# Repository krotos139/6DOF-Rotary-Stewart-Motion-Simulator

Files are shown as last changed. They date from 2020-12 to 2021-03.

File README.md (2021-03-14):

# !!! WARNING !!!

Hey. I'm making 6dof project base of https://github.com/knaufinator/6DOF-Rotary-Stewart-Motion-Simulator/tree/master/Technical

This is a DANGEROUS project, and if absolute care is not taken you will be injured or killed.

Project isn't finished yet. I will place all data to this repo.

# Experiments one

We made PCB from Christopher Knauf. And we can to control one AC motor driver:

<a align="center" href="https://youtu.be/x41-dcpQG4Y
" target="_blank"></a>

# Projects Included
These are the components of the project that are included in this repository

## Technical 

I made all draws in Kompas 3D. I will make drawings in the future.

This is current project:

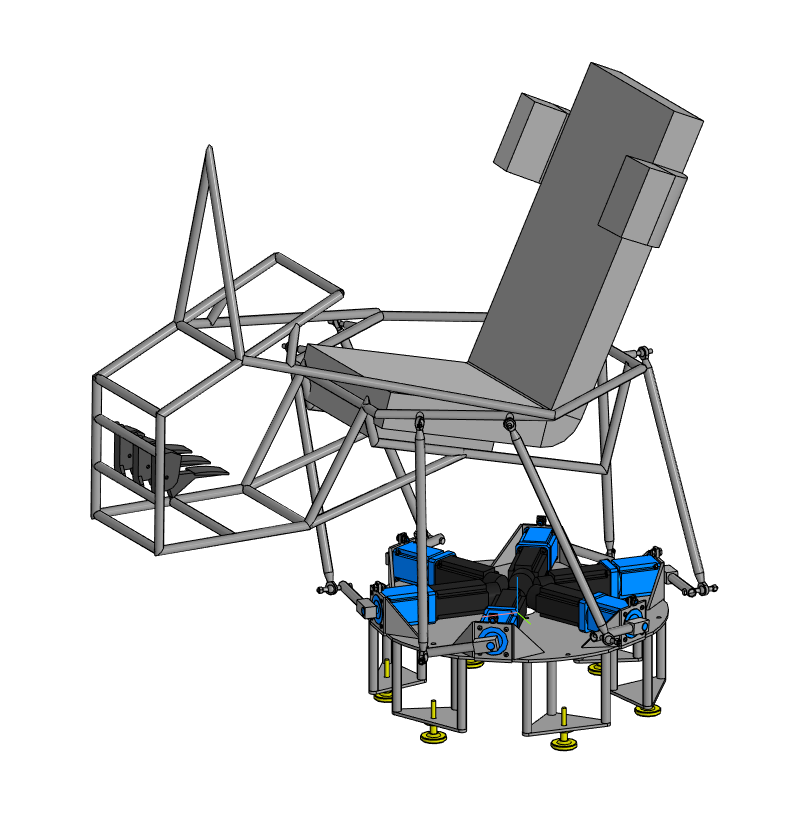
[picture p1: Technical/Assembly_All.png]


## Controller
This is an ESP32 Arduino project. This interfaces with the PC through software like simtools, after correctly configuring. This project utilizes both ESP32 cores in order to maximize refresh rates to 1000Hz, or 1ms interval. A custom MCP23S17 library is included so the outputs of all 6 motors can be set at one time instead of setting them individually, this saves time and allows for more pulses per second. This increase allows for higher movement precision on the rotational arm. There is also a filter library included, this is still in early testing.

## Simtools interface setup
Config for PC to ESP32 USB-> Serial connection within simtools, simtools will be configured to send the 6 axis parameters over to the ESP32 every 1 ms. Over a 250000 baud connection. The packet consists of 6 - 12 bit values, delimited by comma and ended by a "X" Character to signal the ESP32 that the packet is done. 

For simtools you encode the axis representations of x,y,z,Ry,Rx,RZ  with the configuration"Interface - Output" = \<Axis1a>,\<Axis2a>,\<Axis3a>,\<Axis4a>,\<Axis5a>,\<Axis6a>X   

With these settings the software package Simtools or any other custom application may communicate and command the simulator platform to move.



## Controller Schematics

We developed our controller board with optocoupler:

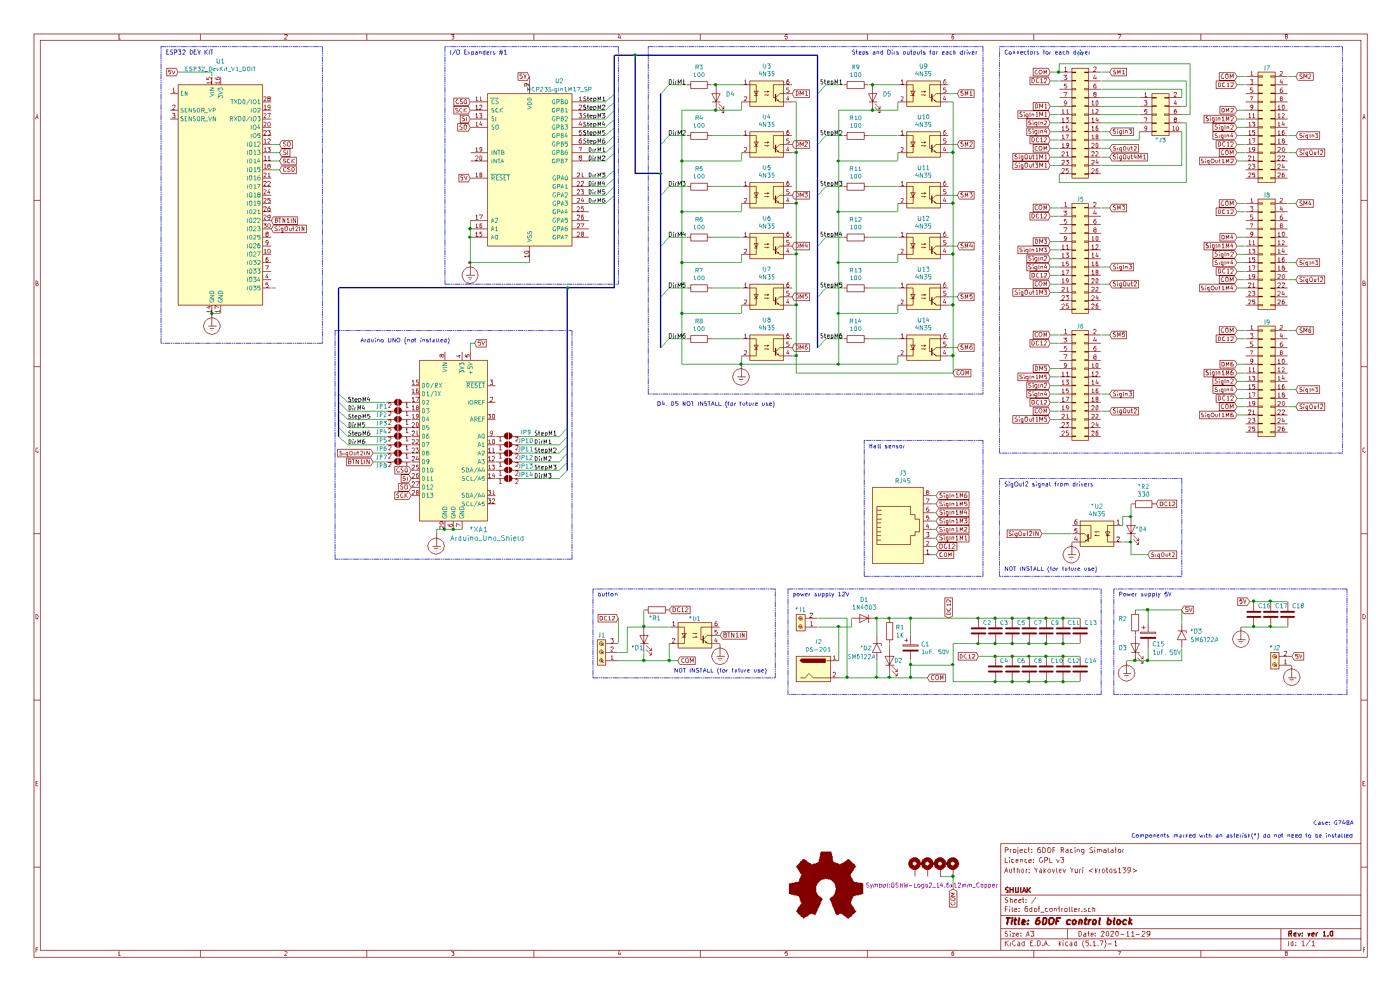
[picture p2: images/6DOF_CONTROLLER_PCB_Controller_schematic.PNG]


We use sensor bord from Christopher Knauf: 

## Controller PCB

We have a problem with USB interface. We start to do second PCB:

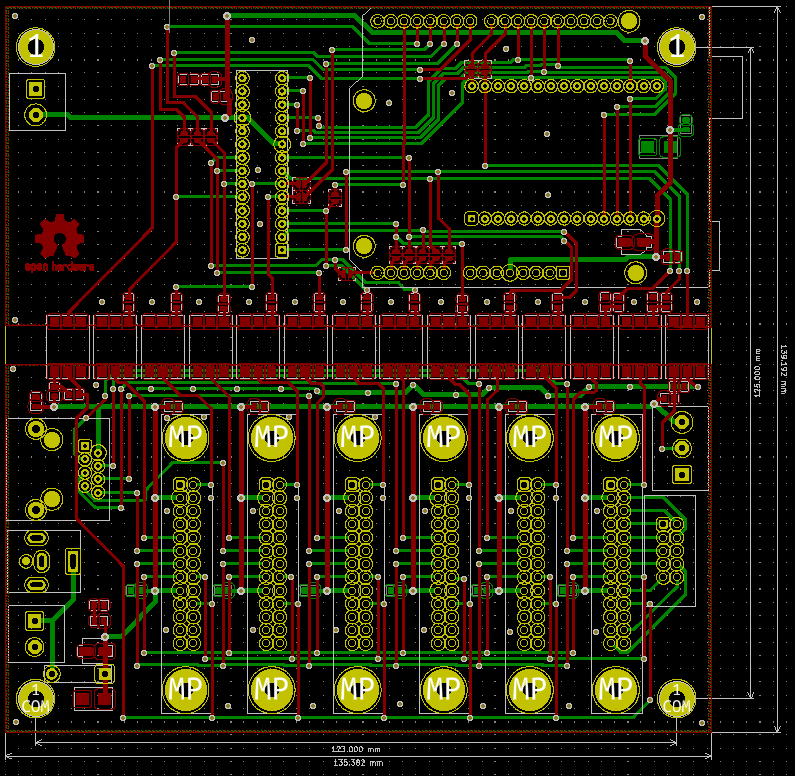
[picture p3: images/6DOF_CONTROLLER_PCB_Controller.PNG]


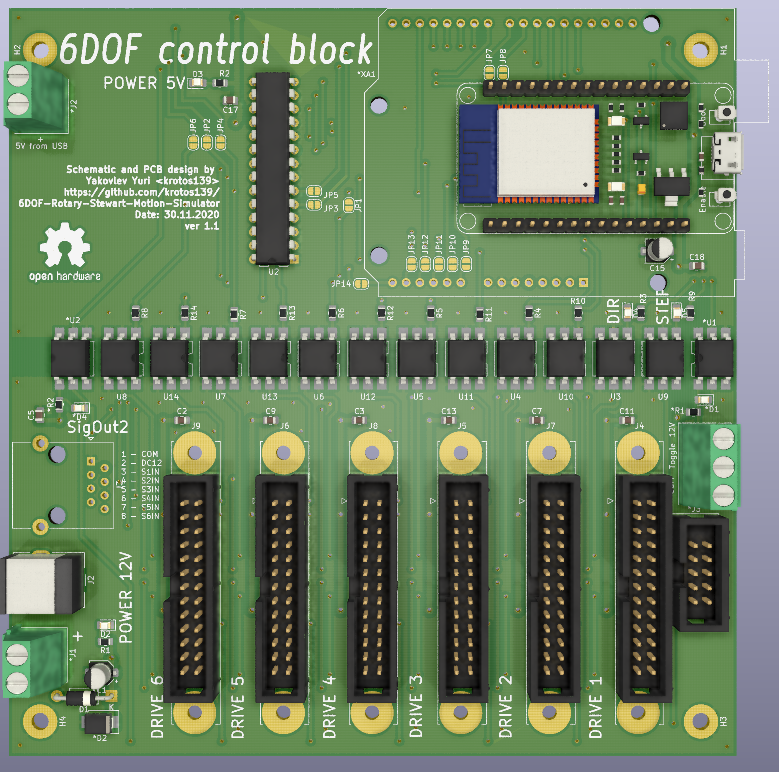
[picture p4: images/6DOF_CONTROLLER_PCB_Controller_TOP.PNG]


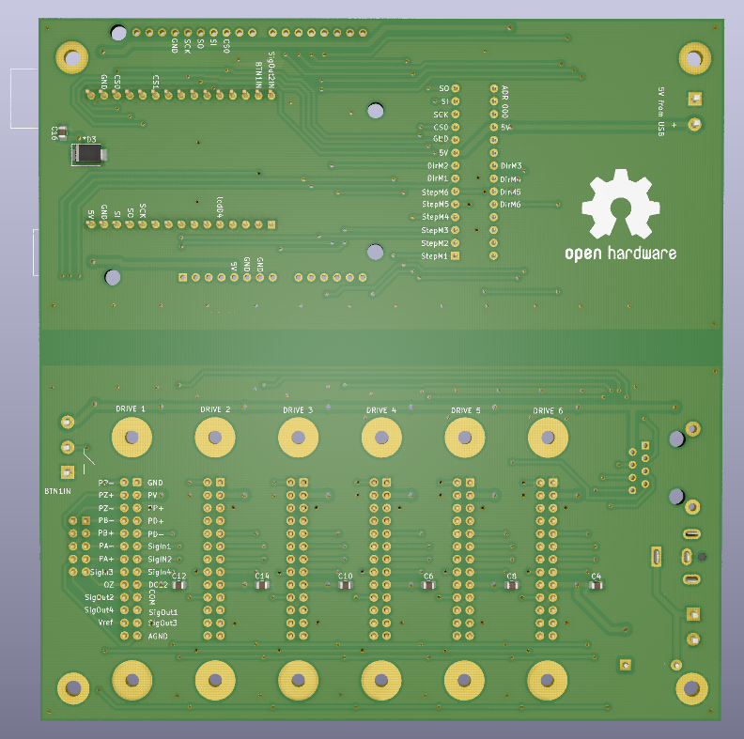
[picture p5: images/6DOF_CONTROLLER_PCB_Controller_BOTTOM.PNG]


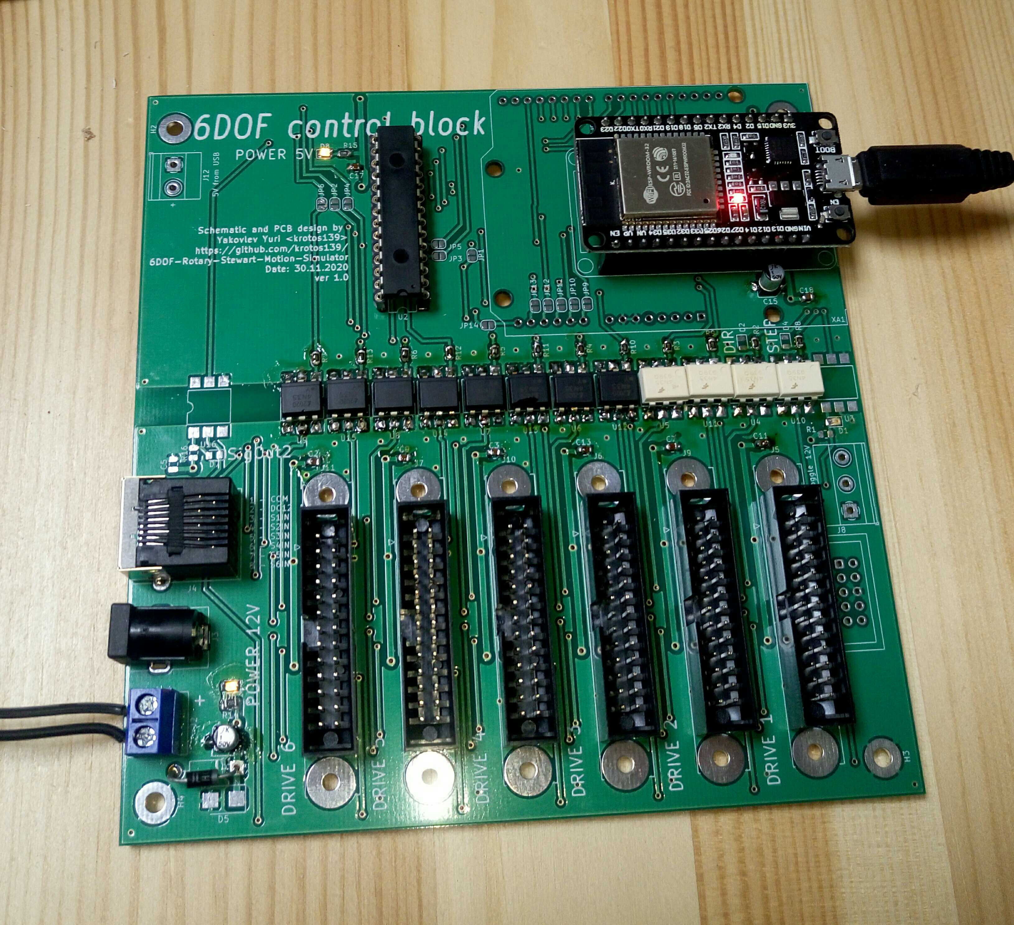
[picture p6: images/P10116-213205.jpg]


## TDD MMOS Schematics

We developed our TDD MMOS board with optocoupler:

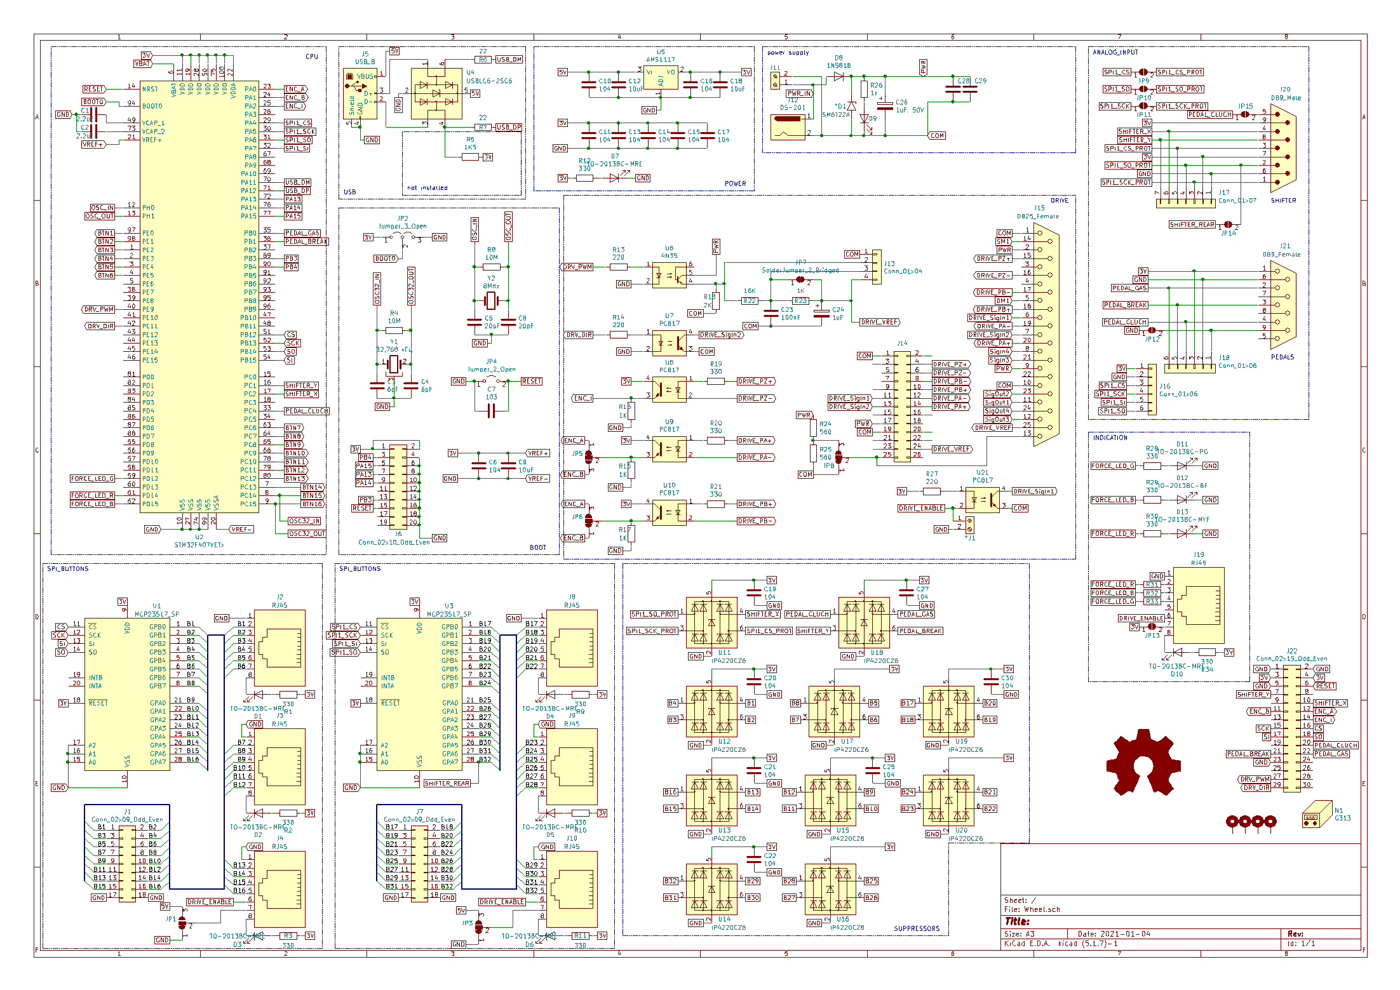
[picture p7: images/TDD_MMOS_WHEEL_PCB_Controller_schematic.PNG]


## TDD MMOS PCB

We redesigned PCB for TDD MMOS. We've added optocouplers and second port extender.

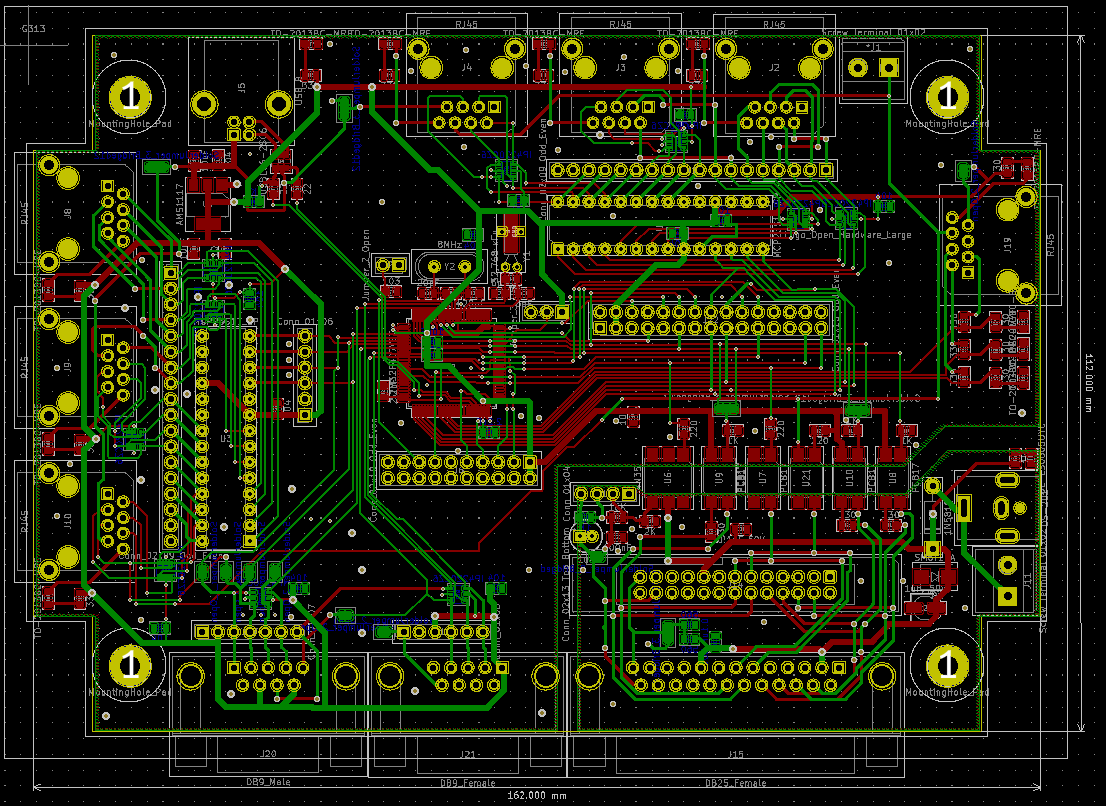
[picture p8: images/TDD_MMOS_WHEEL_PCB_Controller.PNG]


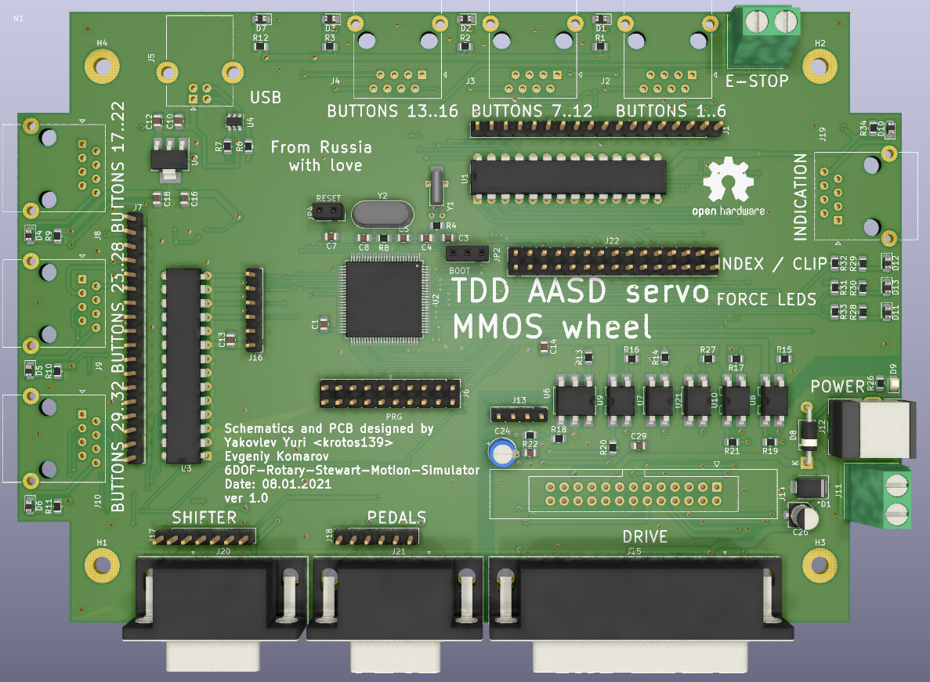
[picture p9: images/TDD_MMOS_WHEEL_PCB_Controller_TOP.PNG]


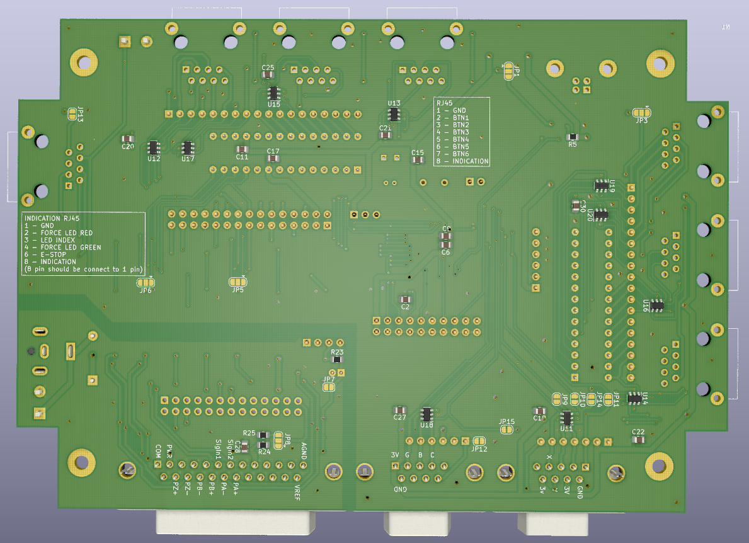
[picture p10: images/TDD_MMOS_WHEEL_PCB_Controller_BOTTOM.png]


## Pedal's PCB

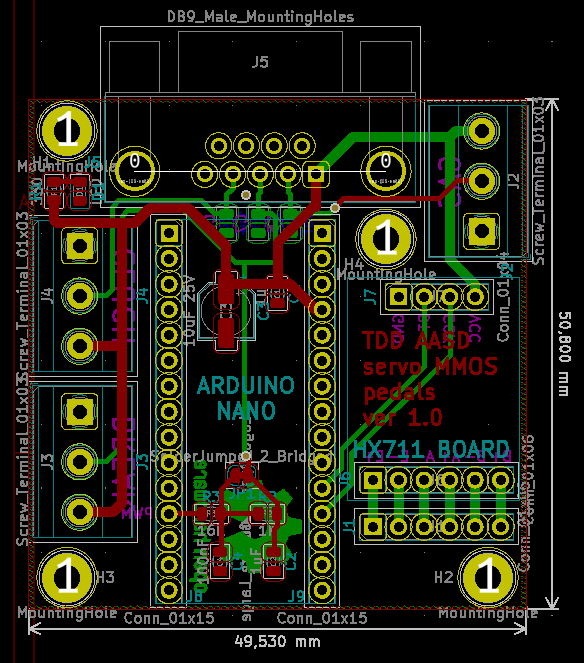
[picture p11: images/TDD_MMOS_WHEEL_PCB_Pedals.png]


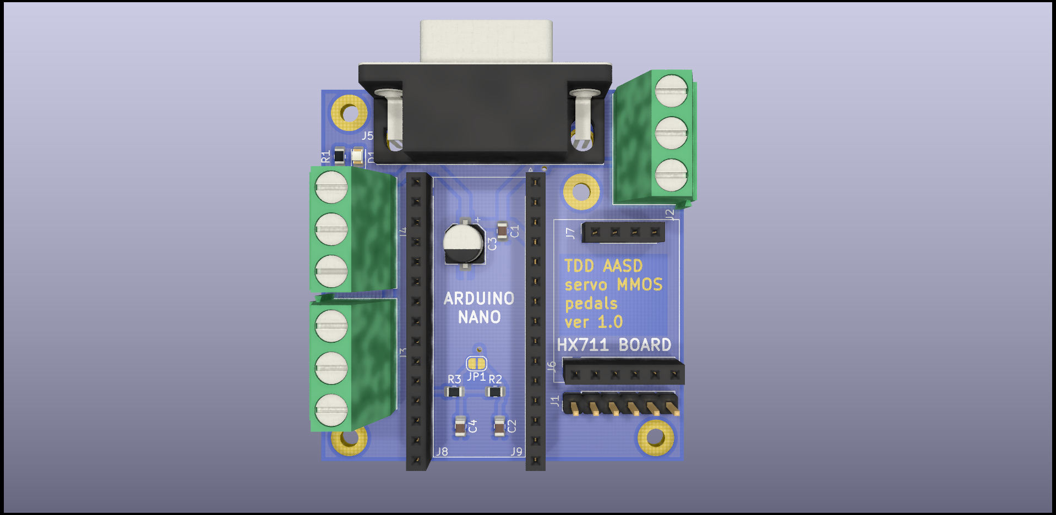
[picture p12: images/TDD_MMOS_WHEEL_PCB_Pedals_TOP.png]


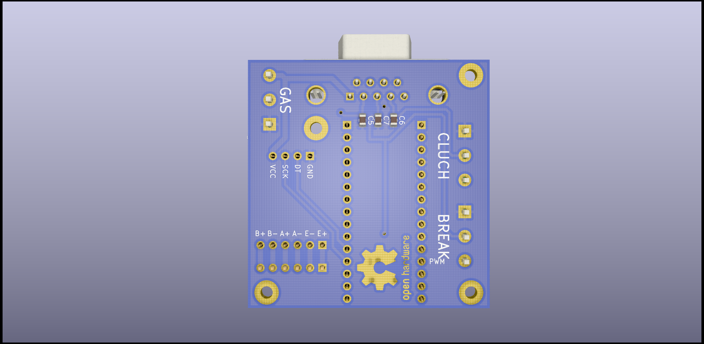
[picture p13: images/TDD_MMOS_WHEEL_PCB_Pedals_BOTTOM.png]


## Platform Test Application
.Net Application for testing position limits and speed of platform. Allows for manual setting of each DOF / Axis. As well works with XBOX360 controller through the PC USB wireless adapter.

# Parts
These are some key parts I used, others can be used in their place, but variations of the AC Servo motor may not be compadible with the PCB, and may require a modified PCB schematic. 

## Electric components

* [AC Ammeter Voltmeter](https://www.aliexpress.com/item/4000589056233.html?spm=a2g0s.9042311.0.0.40e133edW2JAK5)

## Controller 
Main components on the PCB
* [ESP32 Dev board](https://aliexpress.ru/item/1005001267643044.html?spm=a2g0s.9042311.0.0.40e133edW2JAK5) - ESP32 Dev kit
* [MCP23S17-E/SP](https://www.chipdip.ru/product1/8002981432)
* [3.3V to 5V TTL Shifter Module](https://aliexpress.ru/item/32825755943.html?spm=a2g0s.9042311.0.0.40e133edW2JAK5)
* [NJK-5002C NPN NO（Normally Open)Hall Effect Sensor Switch](https://aliexpress.ru/item/32922514991.html?spm=a2g0s.9042311.0.0.40e133edW2JAK5)
* [IDC BOX HEADER 2X13 26PIN](https://aliexpress.ru/item/33009552726.html?spm=a2g0s.9042311.0.0.40e133edW2JAK5)
* [RJ45](https://aliexpress.ru/item/4000226018964.html?spm=a2g0s.9042311.0.0.40e133edW2JAK5)
* [KF301 HEADER 3 pin](https://aliexpress.ru/item/4001057723206.html?spm=a2g0s.9042311.0.0.40e133edW2JAK5)
* [KF301 HEADER 2 pin](https://aliexpress.ru/item/4001057742092.html?spm=a2g0s.9042311.0.0.40e133edW2JAK5)
* [Female Pin Header Connector](https://aliexpress.ru/item/32964870579.html?spm=a2g0s.9042311.0.0.40e133edW2JAK5)

PCB
* [Gerber files](Controller PCB Gerber/)
* [PCB Manufacturer](https://www.rezonit.ru/)

## Base
- Steel plate 8 mm thick 31” diameter
- 6 - Coupler https://amzn.to/2slOiIa

## Drive
* [6 - 750w AC servo Motors](https://www.aliexpress.com/item/32844239563.html)
* [6 - 50:1 Planetary Gears](https://www.aliexpress.com/item/32967571001.html)
*Note ensure planetary gear input diameter matches up to both the motor as well with the coupler output diameter when ordering from Aliexpress

## Connecting Arms

* [12 - Swivel head SA 12mm](https://podtrade.ru/product/42564/)
* [12 - M12 to M10 High Misalignment Angle Reducer Reducers Spacers Rod End Joint](https://www.ebay.com/itm/184116983786)
* 6 - 25x179 Steel pipe

## Swing Arms
* 6 - 25x22mm_clamp2.m3d
* 6 - 25x560 Steel pipe

## Frame 
* 16.5 meters of steel pipe

## Chassis
* [Vesa Monitor mount](https://amzn.to/2TmVS0f)
* [Coped Steel Bungs](https://amzn.to/2TGOcoo)
* [1" OD X .870 ID X .065 Wall Steel tubing](https://amzn.to/3au4FCQ)

## Extras as built in demonstration video
* [LG 34" Ultrawide](https://amzn.to/2t8YvbC)
* [Thrustmaster T16000M FCS](https://amzn.to/30qkHtY)
* [Wind Generator Fan](https://amzn.to/36W1um9)
* [Wind Generator PWM Control](https://amzn.to/2Ns1anq)
* [Wind Generator 90 Degree angle 3"-> 2" Reducer](https://amzn.to/2uN6J9z)
* [Wire Wrap](https://amzn.to/2u3jiNu)

## AC Servo motor settings for 6DoF
These are my settings on the Servo Driver aasd-15a these both enable specific modes as well define the time it should take to accelerate and decelerate the platform before it hits max speed. This is useful for when you want to protect the platform from self destruction due to the fast movements. Make them to large and the platform will feel slugish.
- pn002 - Control Mode - "002" Default
- pn003 - Servo enable - "001"
- pn033 - DSZRtriggermode - "003" Power on automatically
- pn034 - The origin return reference point model - "001" Inversion for REF(rising along the trigger)as a reference point
- pn035 - The origin back to the origin model - "000" Default
- pn036 - The origin position offset high - "011" ten thousand pulse
- pn037 - The origin position offset low - "5000" pulse
- pn038 - The origin back to the first speed - "100" R/min
- pn039 - The origin back to the second speed - "100" R/min
- pn040 - The accelerating time of origin - "050" Default
- pn041 - The origin return to slow down time - "050" Default
- pn042 - The origin in the delay - "100" ms
- pn043 - Complete the signal delay of origin - "080" Default
- pn044 - The origin return instruction execution mode - "000" Default
- pn052 - SigIn1 is "REF" - "023"
- pn053 - SigIn2 is "PSTOP" - "027"
- pn054 - SigIn3 is "PClear" - "019"
- pn055 - SigIn4 is "INH" - "020"
- pn098 - Gear - "80"
- pn109 - Position command deceleration mode- "002"
- pn110 - Position command a filtering time constant - "050"
- pn111 - S-shaped filtering time constant Ta position instruction - "50"
- pn112 - position instruction Ts S-shaped filtering

time constant Ts - "50"

Default settings:
- pn002 - Control Mode - "002"
- pn003 - Servo enable - "000"
- pn033 - DSZRtriggermode - "000"
- pn034 - The origin return reference point model - "000"
- pn035 - The origin back to the origin model - "000"
- pn036 - The origin position offset high - "000"
- pn037 - The origin position offset low - "0000"
- pn038 - The origin back to the first speed - "200" R/min
- pn039 - The origin back to the second speed - "50" R/min
- pn040 - The accelerating time of origin - "050"
- pn041 - The origin return to slow down time - "050"
- pn042 - The origin in the delay - "60" ms
- pn043 - Complete the signal delay of origin - "080"
- pn044 - The origin return instruction execution mode - "000"
- pn052 - SigIn1 is "REF" - "001"
- pn053 - SigIn2 is "PSTOP" - "002"
- pn054 - SigIn3 is "PClear" - "019"
- pn055 - SigIn4 is "INH" - "008"
- pn098 - Gear - "1"
- pn109 - Position command deceleration mode- "001"
- pn110 - Position command a filtering time constant - "050"
- pn111 - S-shaped filtering time constant Ta position instruction - "50"
- pn112 - position instruction Ts S-shaped filtering - "20"

## AC Servo motor settings for Wheel

- PN002 = 0	(control mode - voltage mode, requires restart) (Default:02)
- PN003 = 0	( Servo enabled? - external) (Default:00)
- PN018 = 0	(Take the encoder output pulse AB phase logic - 0-1) (Default:00)
- PN051 = 1500	(Motor max RPM - see motor specs) (Default:3000)
- PN053 = 18? 	(SigIn 2 port functional allocation  -27 - 27) - 58? "command reverse" function number range name
- PN188 = 159	(Analog torque instruction smooth filtering time - 1-500ms) (Default:5)
- PN189 = 39 	(Analog torque instruction gain 1-300 %/V) (Default:30)
- PN190 = 0	(Analog torque instruction offset adjustment  -1.5v - 1.5v) (Default:0)
- PN191 = 1	(Simulation of torque command direction - try 0 first) (Default:0)
- PN198 = 120 	(Torque control speed limit - 0-4500rpm) (Default:2500)

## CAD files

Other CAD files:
Technical/Drawing/base_part1_support.dxf
Technical/DWG/base_part2.dwg
Technical/Drawing/base_part1.dxf
Technical/DWG/base_part1_support.dwg
Technical/Drawing/base_part2.dxf
Technical/DWG/base_part1.dwg

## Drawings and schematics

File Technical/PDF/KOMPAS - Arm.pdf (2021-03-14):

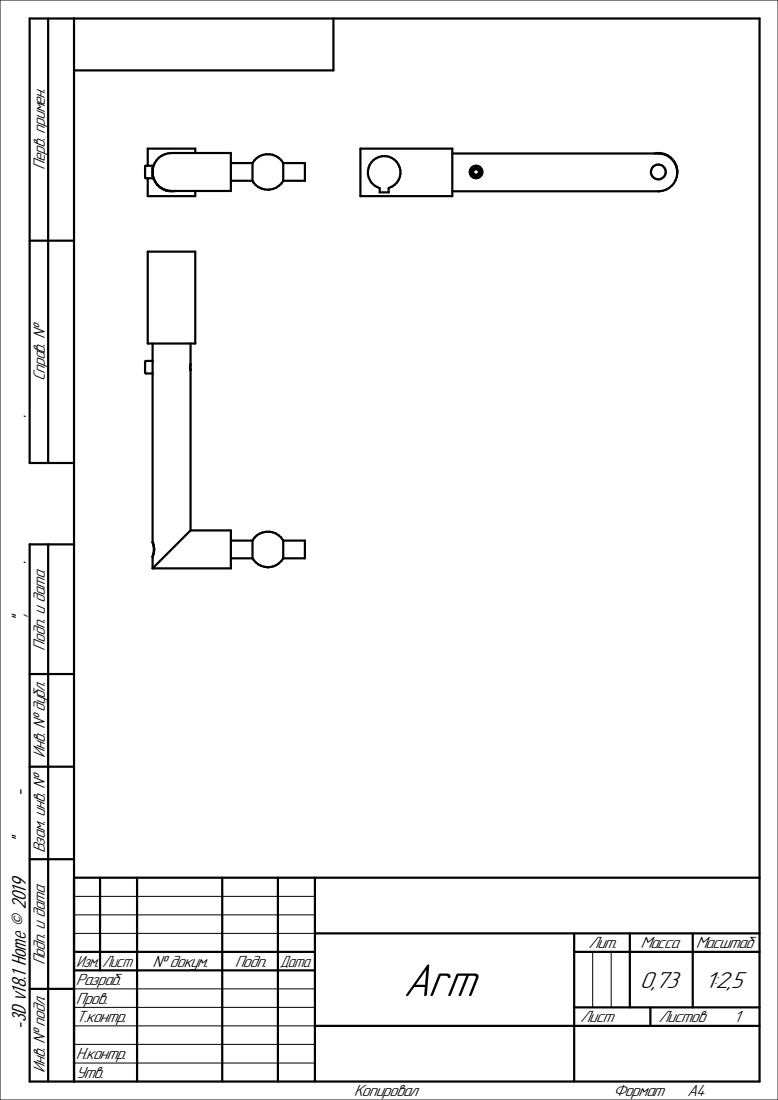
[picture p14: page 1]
Н.контр. Утв.; Копировал; Формат

Инв. № подл. Подп. и дата Взам. инв. № Инв. № дубл. Подп. и дата Справ. № Перв. примен. Не для коммерческого использования

КОМПАС-3D v18.1 Home © 2019 ООО "АСКОН-Системы проектирования", Россия. Все права защищены.

Arm | Лит. | Масса | Масштаб

Изм. | Лист | № докум. | Подп. | Дата | | | | | 0,73
Разраб. Пров. Т.контр.

Лист | Листов

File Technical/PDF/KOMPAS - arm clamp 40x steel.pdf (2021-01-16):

А | А

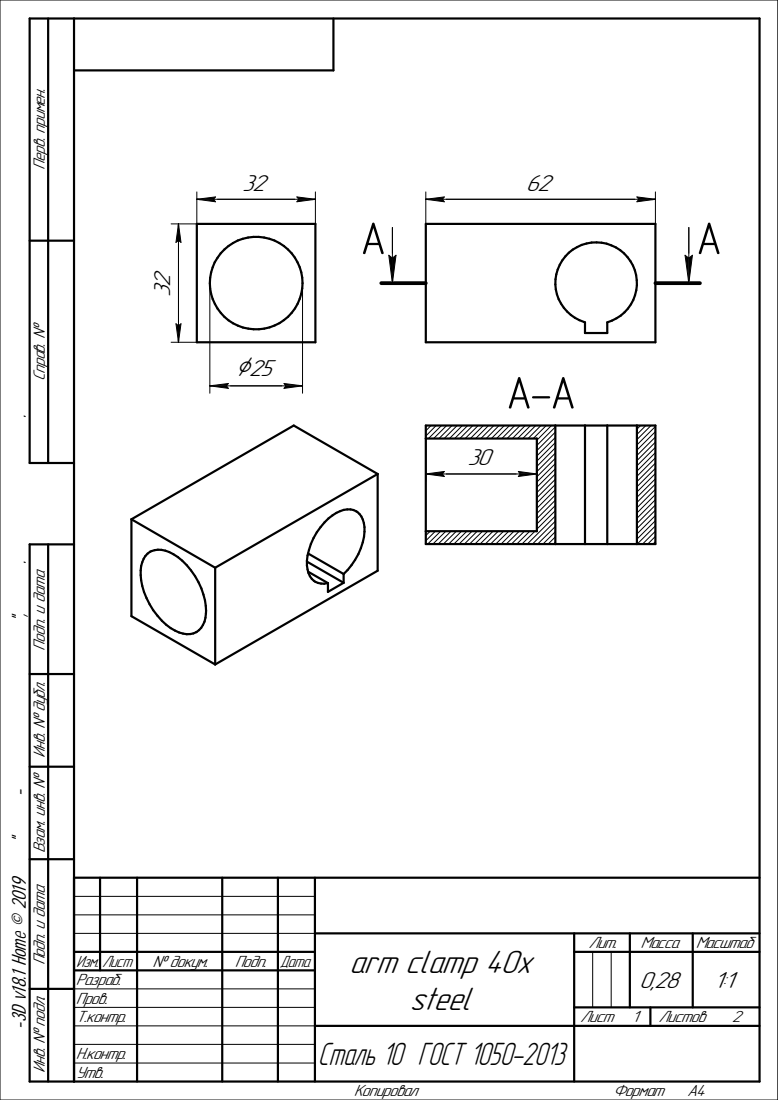
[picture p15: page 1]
Инв. №; подл. Подп. и; дата; Взам. инв. №; дубл. Подп. и; Справ. №

Перв. примен. Не для коммерческого использования Копировал Формат A4

КОМПАС-3D v18.1 Home © 2019 ООО "АСКОН-Системы проектирования", Россия. Все права защищены.

steel | Лит. | Масса | Масштаб

Изм. Лист | № докум. | Подп. | Дата | | | | | 0,28 | 1:1 arm clamp 40x
Разраб.
Пров.
Т.контр. | | | | Лист 1 | Листов 2

Н.контр.
Утв.

Сталь 10 ГОСТ 1050-2013

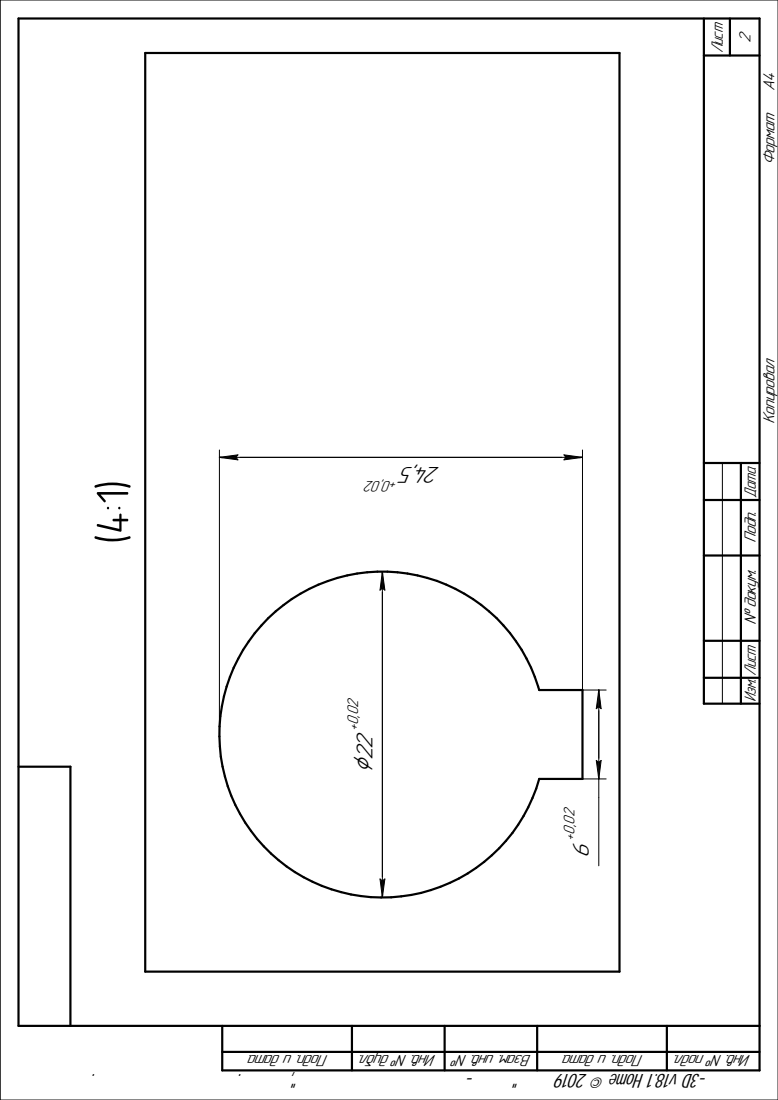
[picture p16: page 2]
Лист; Изм. Лист; Копировал; Формат

докум. Подп. Дата

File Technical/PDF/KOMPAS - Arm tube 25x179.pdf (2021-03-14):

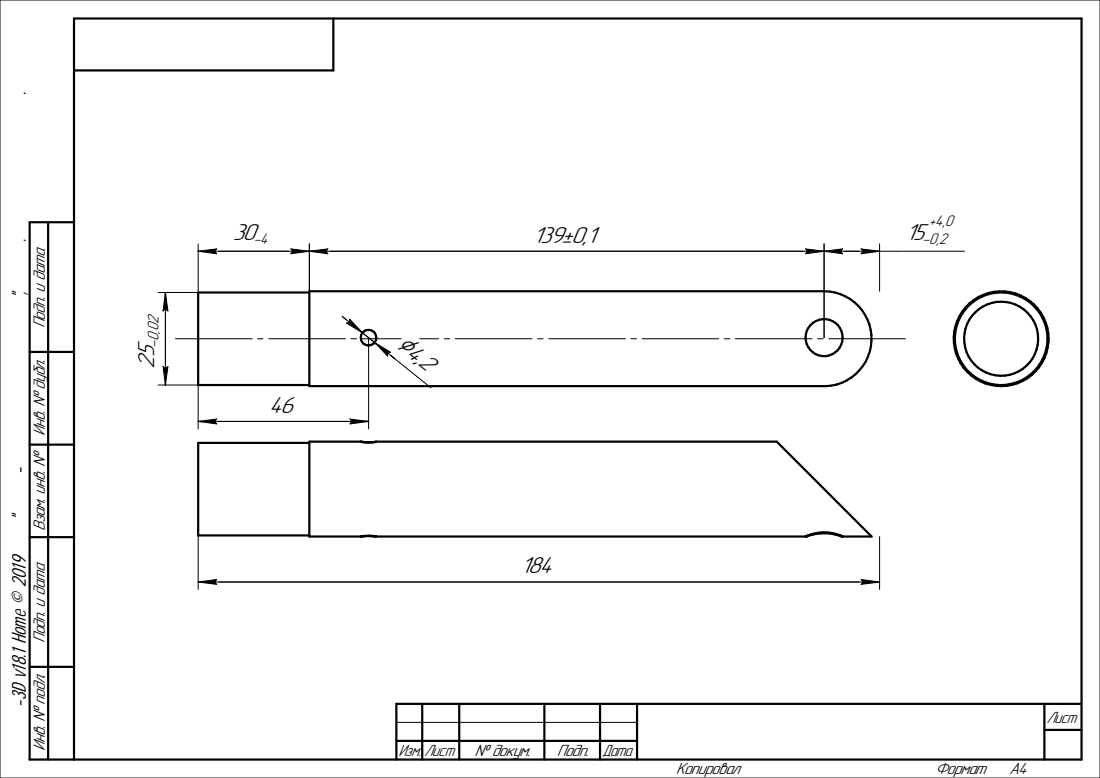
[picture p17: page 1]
Лист; Изм. Лист; докум.; Подп.; Дата; Копировал; Формат

КОМПАС-3D v18.1 Home © 2019 ООО "АСКОН-Системы проектирования", Россия. Все права защищены.

Инв. № подл. Подп. и дата Взам. инв. № Инв. № дубл. Подп. и дата Не для коммерческого использования

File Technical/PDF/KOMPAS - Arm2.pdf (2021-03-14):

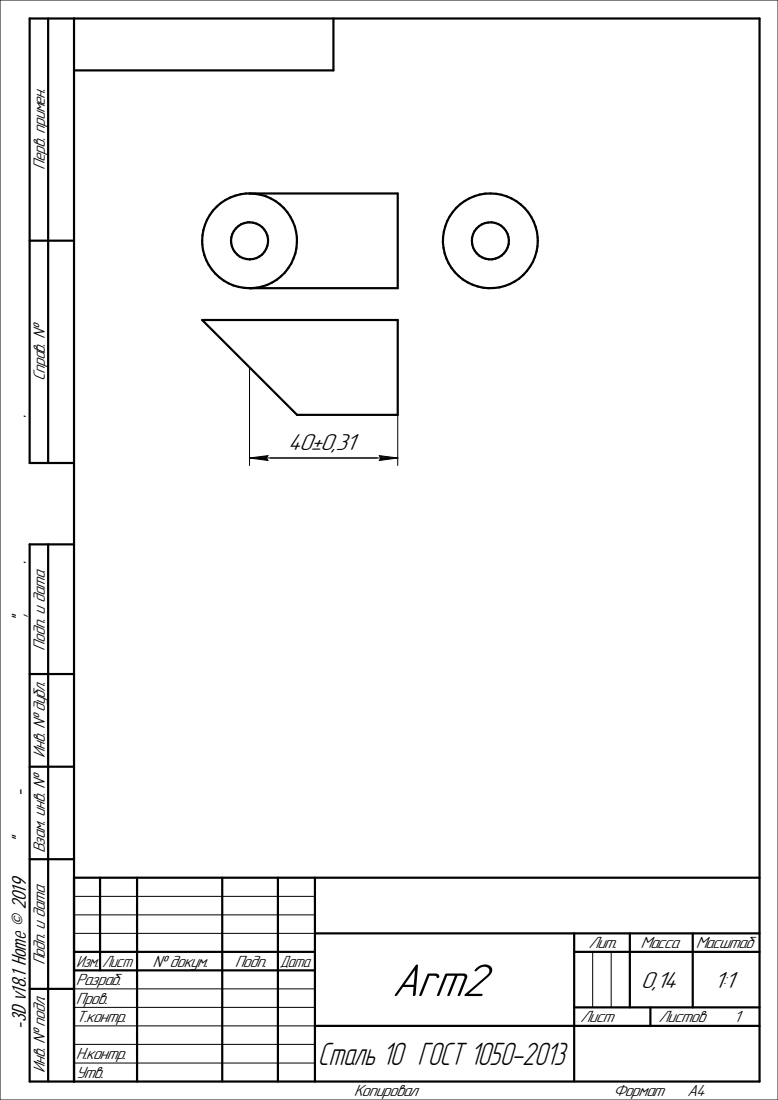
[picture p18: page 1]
Инв. №; подл. Подп. и; дата; Взам. инв. №; дубл. Подп. и; Справ. №

Перв. примен. Не для коммерческого использования Копировал Формат A4

КОМПАС-3D v18.1 Home © 2019 ООО "АСКОН-Системы проектирования", Россия. Все права защищены.

Arm2 | Лит. | Масса | Масштаб

Изм. Лист | № докум. | Подп. | Дата | | | | | 0,14 | 1:1
Разраб.
Пров.
Т.контр. | | | | Лист | Листов 1

Н.контр.
Утв.

Сталь 10 ГОСТ 1050-2013

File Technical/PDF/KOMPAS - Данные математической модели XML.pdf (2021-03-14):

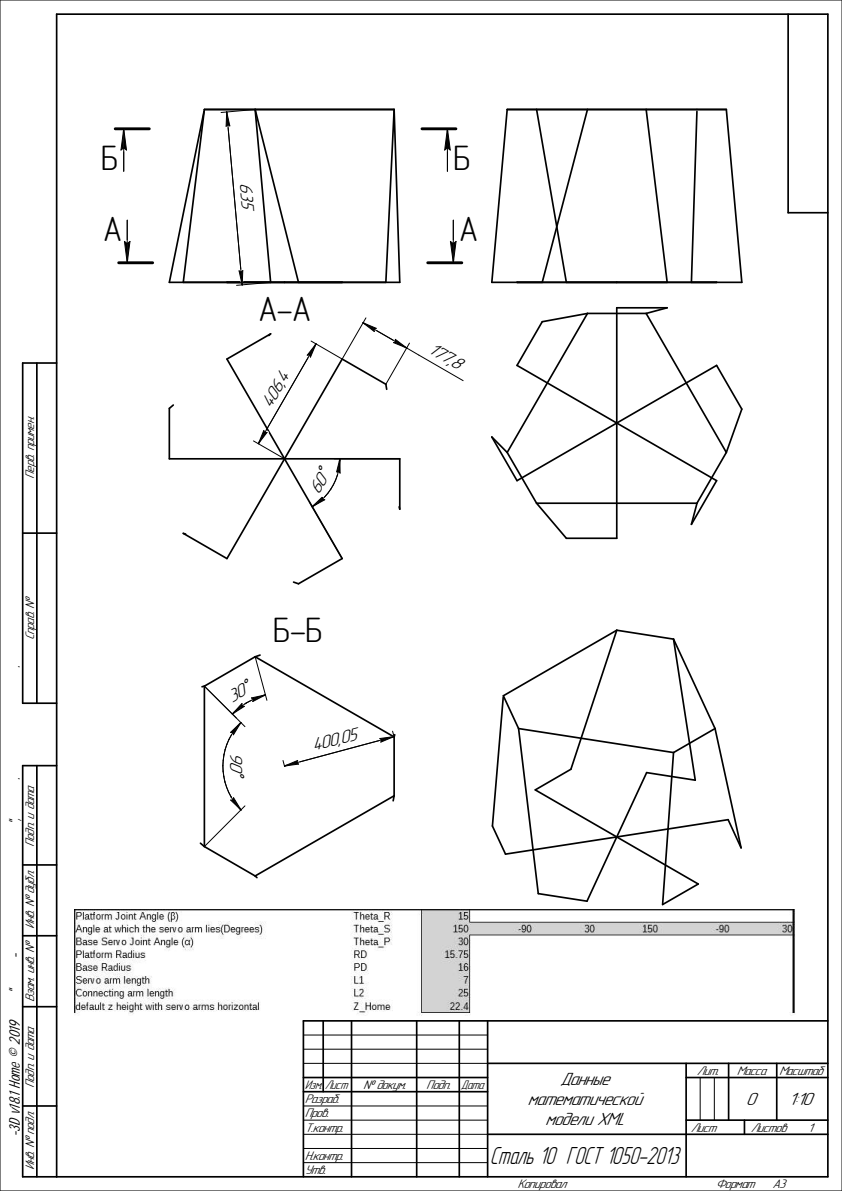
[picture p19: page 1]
Копировал; Формат

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

КОМПАС-3D v18.1 Home © 2019 ООО "АСКОН-Системы проектирования", Россия. Все права защищены.

Данные математической модели XML | Лит. | Масса | Масштаб

Изм. | Лист | № докум. | Подп. | Дата | | | | | 0
Разраб. Пров. Т.контр.

Лист | Листов

Сталь 10 ГОСТ 1050-2013

Н.контр. Утв.

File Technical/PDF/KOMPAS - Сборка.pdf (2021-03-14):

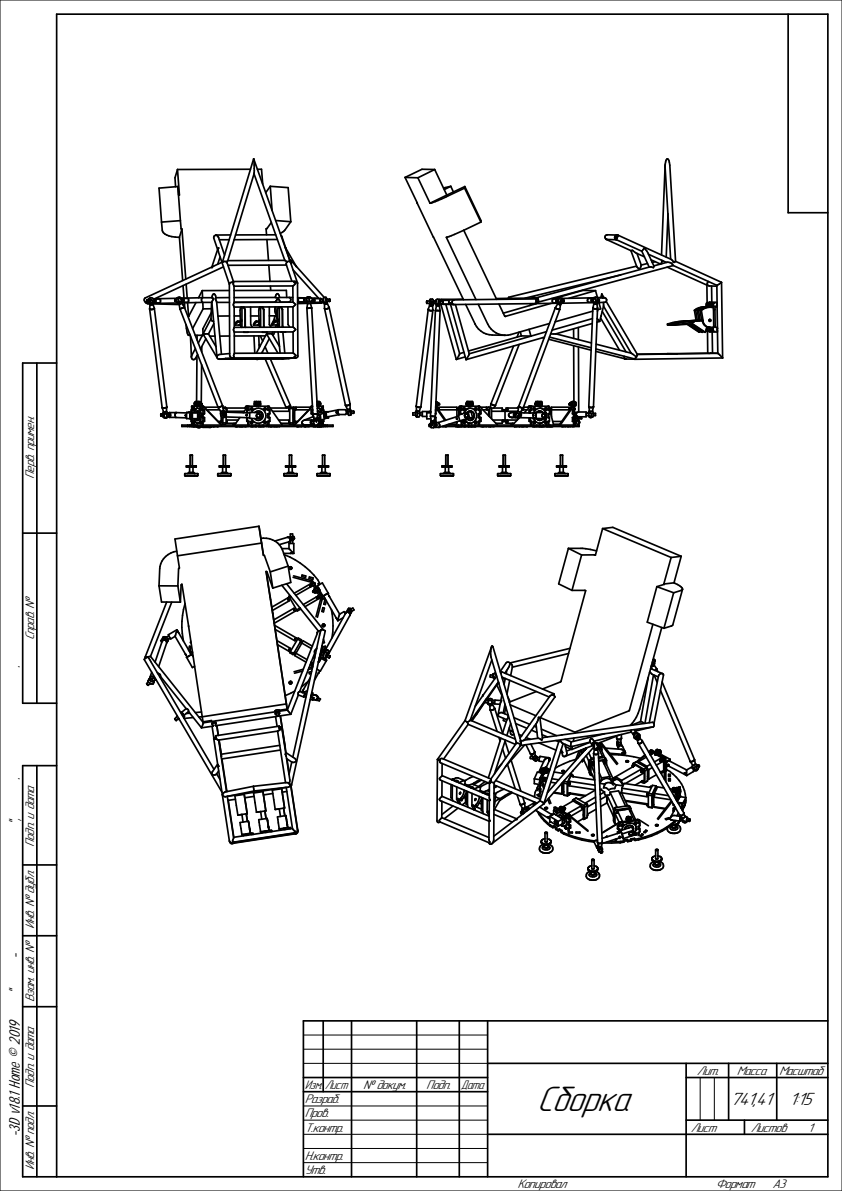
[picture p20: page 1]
Масса; Масштаб; докум.; Подп.; Дата; Лит.; Лист; Листов; Н.контр. Утв.; Сборка; Копировал; Формат

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

КОМПАС-3D v18.1 Home © 2019 ООО "АСКОН-Системы проектирования", Россия. Все права защищены.

Изм.
Лист
Разраб. Пров. Т.контр.

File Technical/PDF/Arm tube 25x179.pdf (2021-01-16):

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

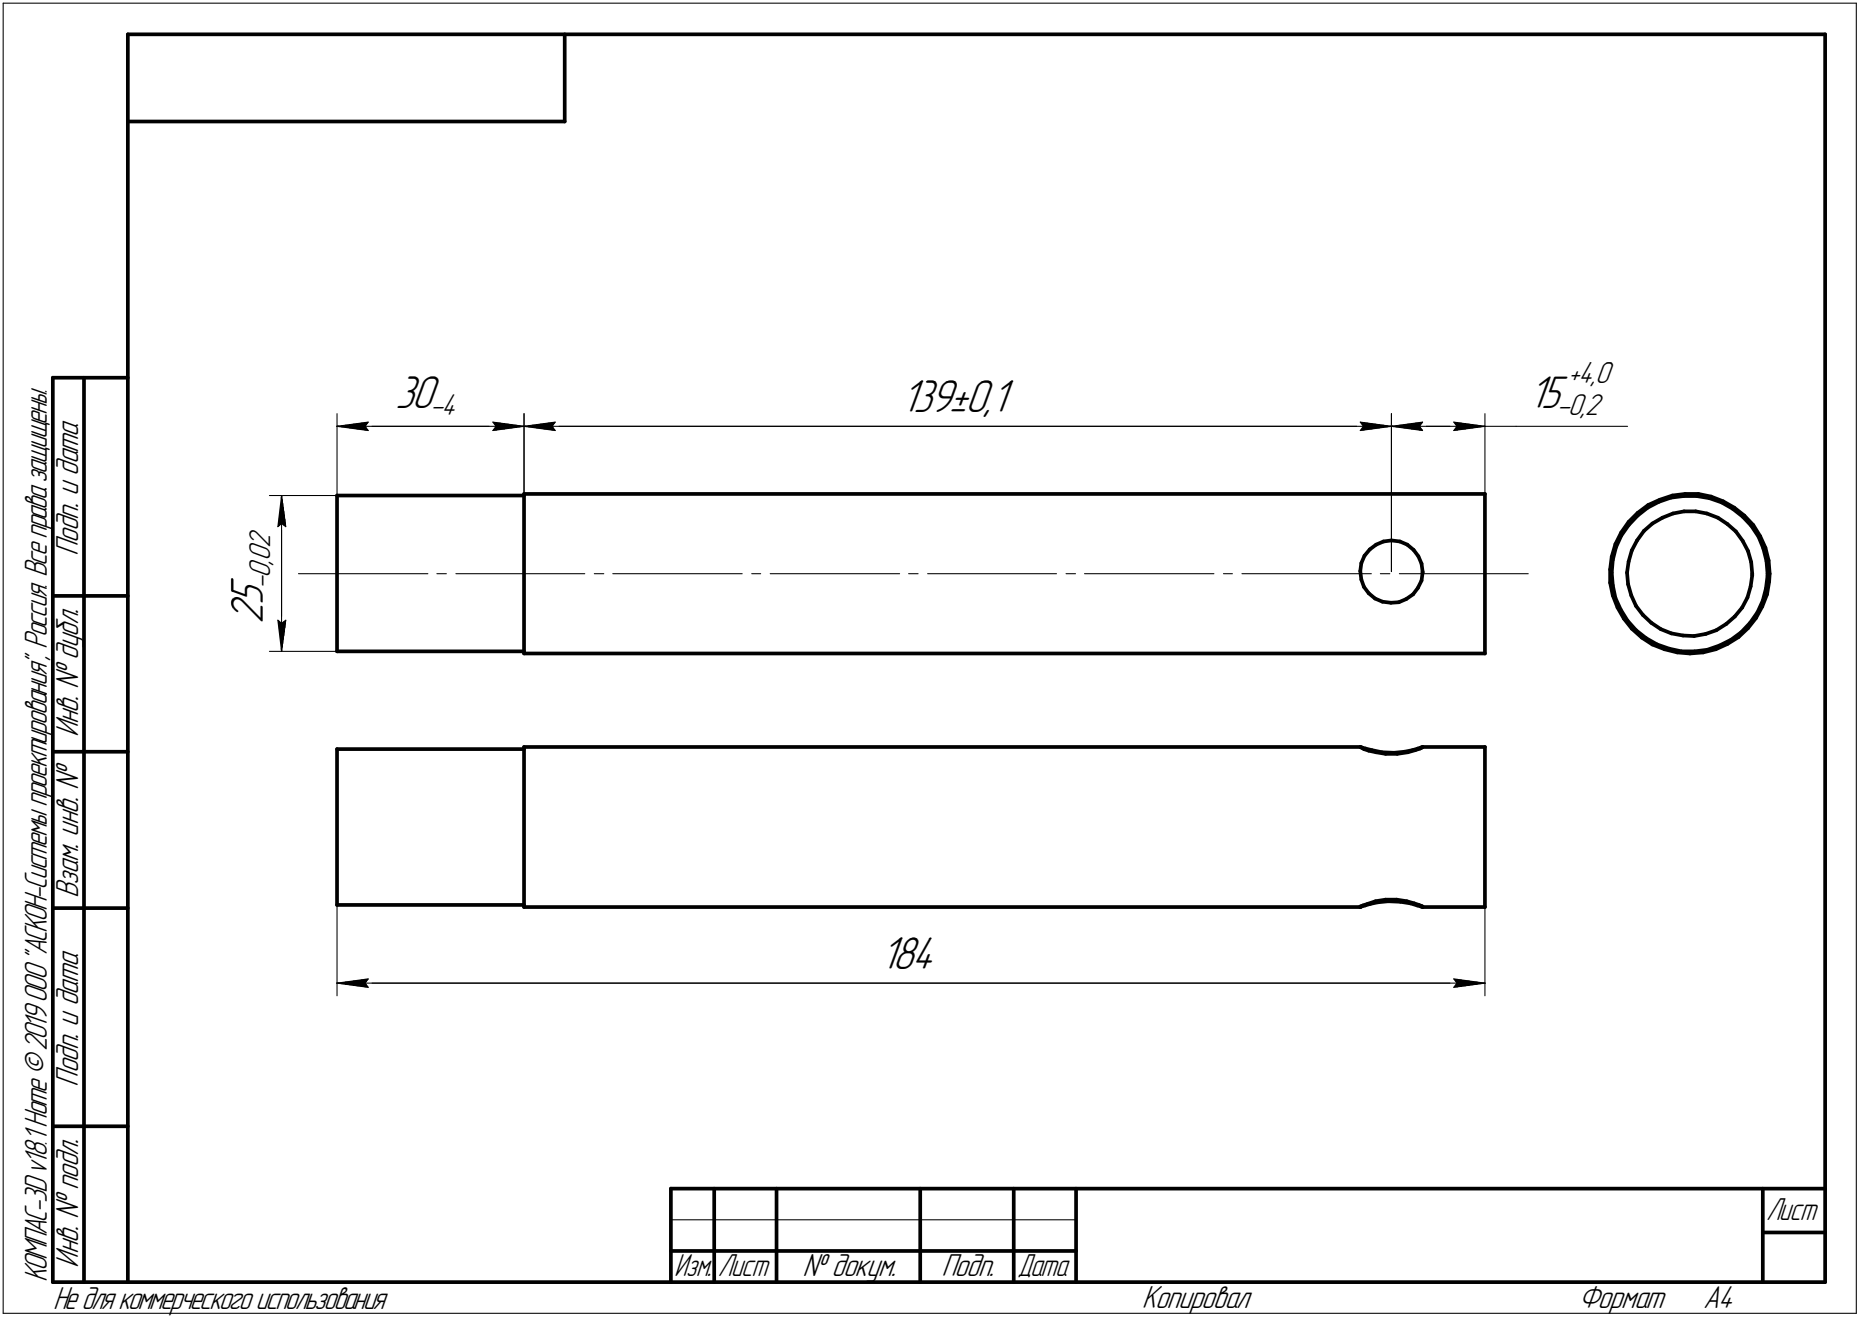
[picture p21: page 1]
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

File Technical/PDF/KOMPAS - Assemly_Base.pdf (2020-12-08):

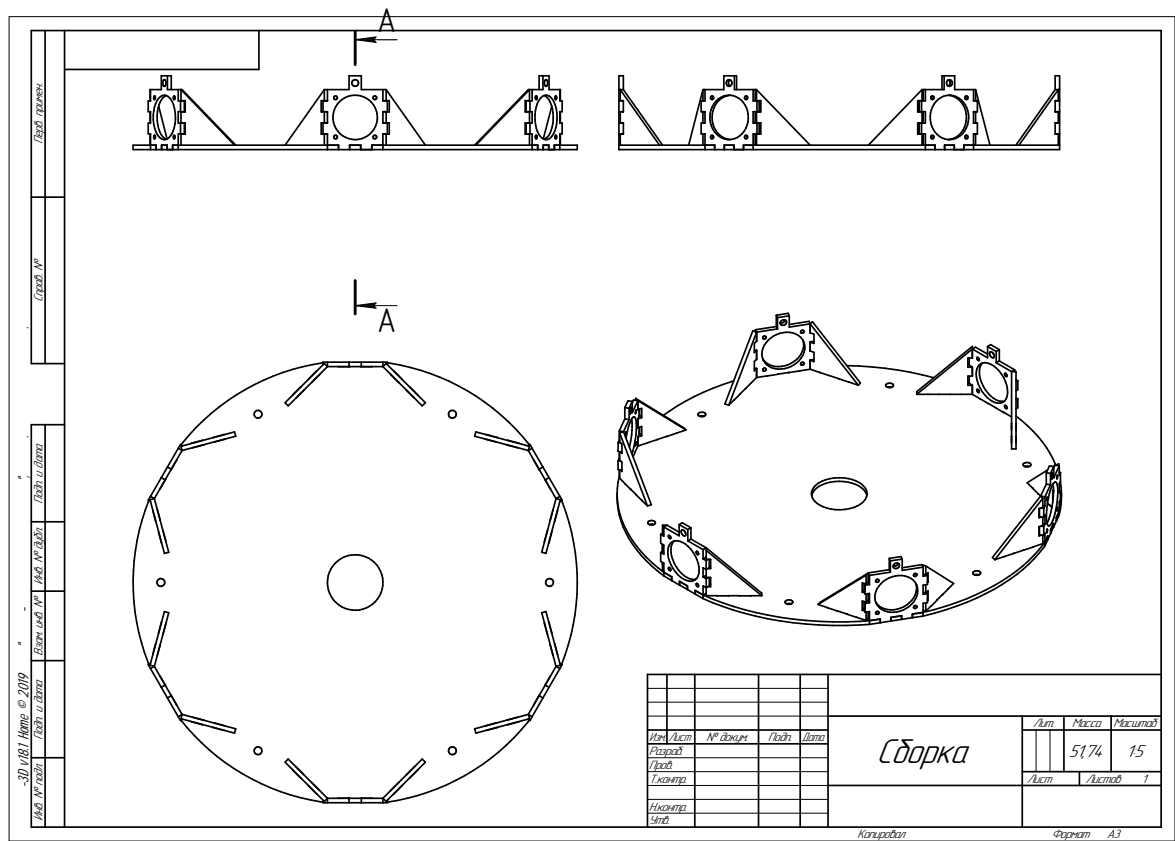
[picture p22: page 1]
Н.контр. Утв.; Копировал; Формат

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

КОМПАС-3D v18.1 Home © 2019 ООО "АСКОН-Системы проектирования", Россия. Все права защищены.

Сборка | Лит. | Масса | Масштаб

Изм. | Лист | № докум. | Подп. | Дата | | | | | 51,74 | 1:5 1
Разраб. Пров. Т.контр.

Лист | Листов

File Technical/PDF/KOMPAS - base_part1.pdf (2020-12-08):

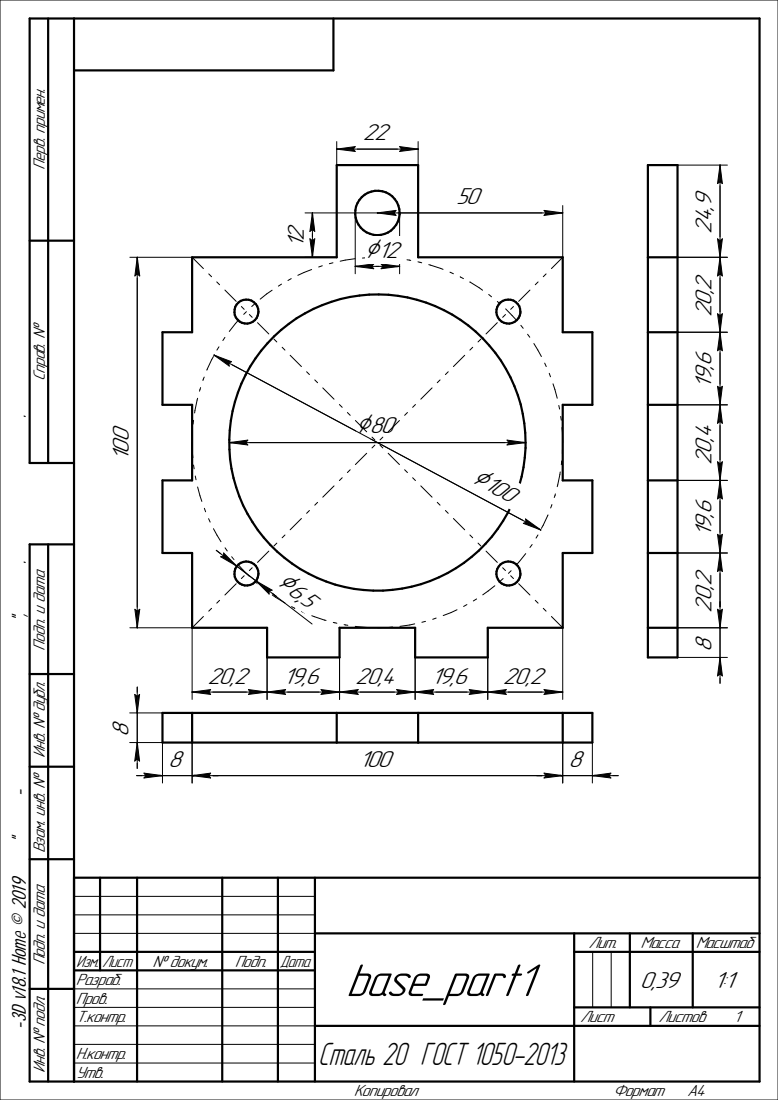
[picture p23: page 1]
Инв. №; подл. Подп. и; дата; Взам. инв. №; дубл. Подп. и; Справ. №

Перв. примен. Не для коммерческого использования Копировал Формат A4

КОМПАС-3D v18.1 Home © 2019 ООО "АСКОН-Системы проектирования", Россия. Все права защищены.

base_part1 | Лит. | Масса | Масштаб

Изм. Лист | № докум. | Подп. | Дата | | | | | 0,39 | 1:1
Разраб.
Пров.
Т.контр. | | | | Лист | Листов 1

Н.контр.
Утв.

Сталь 20 ГОСТ 1050-2013

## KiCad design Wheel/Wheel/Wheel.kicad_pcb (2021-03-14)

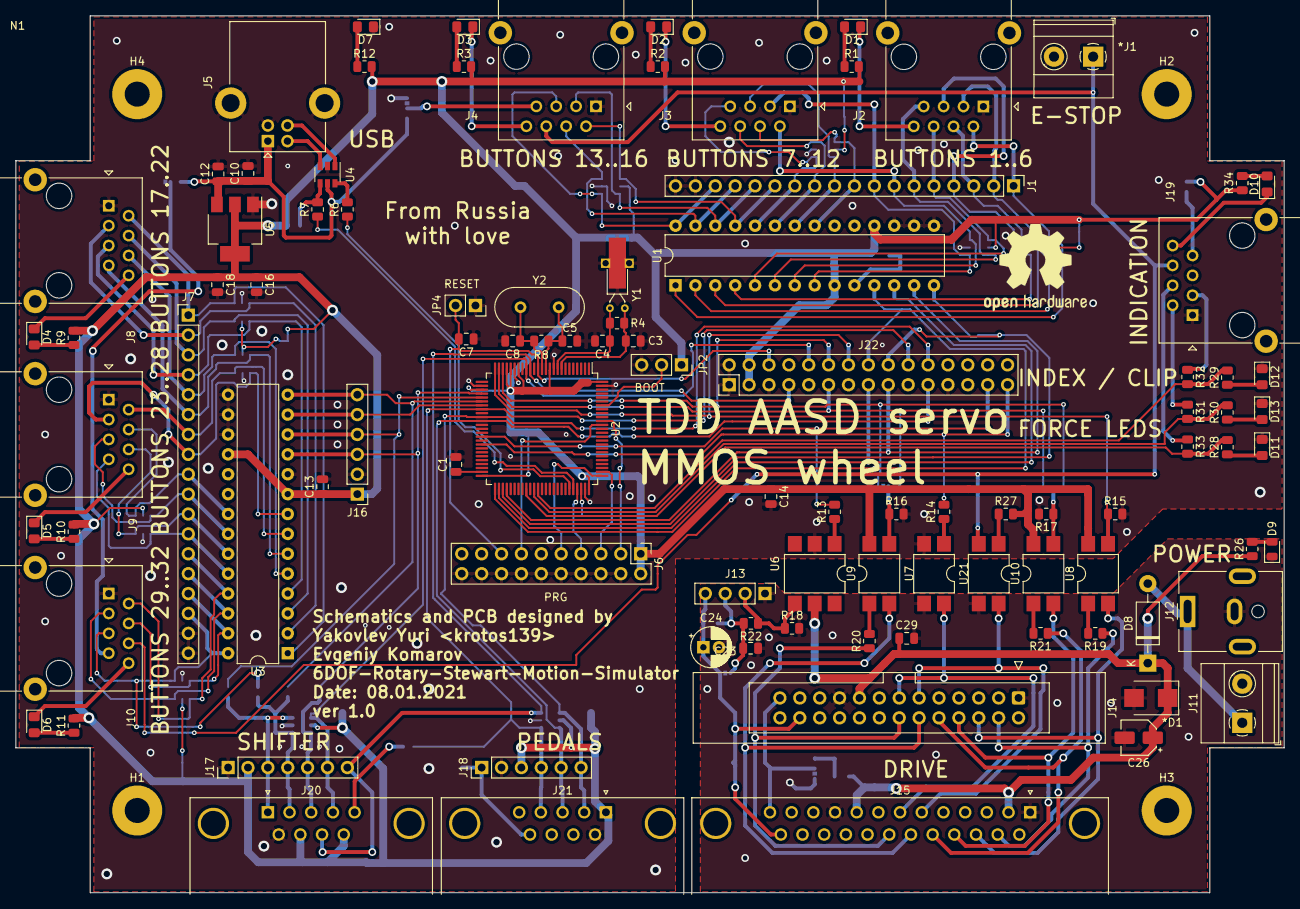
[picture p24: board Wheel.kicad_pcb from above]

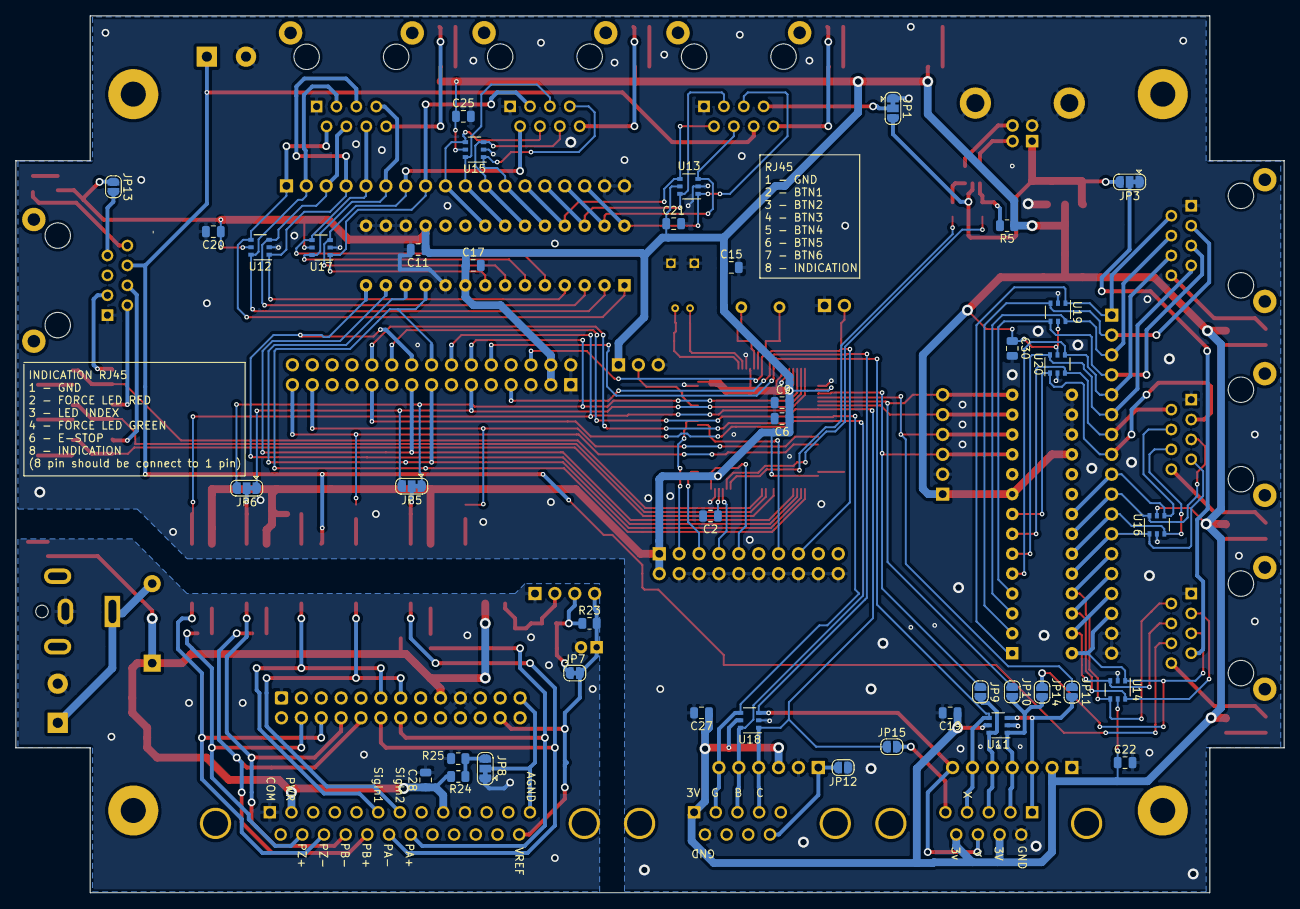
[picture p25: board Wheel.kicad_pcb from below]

Board: 2 copper layers, 162.0 x 112.0 mm, 145 parts (41 on the bottom side), 130 nets.

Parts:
*D1: SM6T22A; D_SMB
*J1: Screw_Terminal_01x02; TerminalBlock_Phoenix_MKDS-1,5-2_1x02_P5.00mm_Horizontal
C1, C2: 2.2uF; C_0805_2012Metric
C3, C4: 6pF; C_0805_2012Metric
C5, C8: 20pF; C_0805_2012Metric
C6, C10, C11, C13, C14, C15, C16, C17, C19, C20, C21, C22, C25, C27, C30: 104; C_0805_2012Metric
C7: 103; C_0805_2012Metric
C9, C12, C18: 10uF; C_0805_2012Metric
C23: 100nF; C_0805_2012Metric
C24: 1uF; CP_Radial_D5.0mm_P2.00mm
C26: 1uF, 50V; CP_Elec_4x5.7
C28, C29: 0.1uF 50V; C_0805_2012Metric
D1, D2, D3, D4, D5, D6, D7, D10: TO-2013BC-MRE; D_0805_2012Metric_Pad1.15x1.40mm_HandSolder
D8: 1N5818; D_DO-41_SOD81_P10.16mm_Horizontal
D9: BL-LS0805UYC; LED_0805_2012Metric
D11: TO-2013BC-PG; D_0805_2012Metric_Pad1.15x1.40mm_HandSolder
D12: TO-2013BC-BF; D_0805_2012Metric_Pad1.15x1.40mm_HandSolder
D13: TO-2013BC-MYF; D_0805_2012Metric_Pad1.15x1.40mm_HandSolder
H1, H2, H3, H4: MountingHole_Pad; MountingHole_3.2mm_M3_Pad
J1, J7: Conn_02x09_Odd_Even; PinHeader_1x18_P2.54mm_Vertical
J2, J3, J4, J8, J9, J10, J19: RJ45; RJ45_Ninigi_GE
J5: USB_B; USB_B_Lumberg_2411_02_Horizontal
J6: Conn_02x10_Odd_Even; PinHeader_2x10_P2.54mm_Vertical
J11: Screw_Terminal_01x02; TerminalBlock_Phoenix_MKDS-1,5-2_1x02_P5.00mm_Horizontal
J12: DS-201; BarrelJack_CUI_PJ-063AH_Horizontal
J13: Conn_01x04; PinHeader_1x04_P2.54mm_Vertical
J14: Conn_02x13_Top_Bottom; IDC-Header_2x13_P2.54mm_Latch_Vertical
J15: DB25_Female; DSUB-25_Female_Horizontal_P2.77x2.84mm_EdgePinOffset7.70mm_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
J16, J18: Conn_01x06; PinHeader_1x06_P2.54mm_Vertical
J17: Conn_01x07; PinHeader_1x07_P2.54mm_Vertical
J20: DB9_Male; DSUB-9_Male_Horizontal_P2.77x2.84mm_EdgePinOffset7.70mm_Hou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
J21: DB9_Female; DSUB-9_Female_Horizontal_P2.77x2.84mm_EdgePinOffset7.70mm_H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
J22: Conn_02x15_Odd_Even; PinHeader_2x15_P2.54mm_Vertical
JP1, JP3, JP5, JP6, JP8: SolderJumper_3_Bridged12; SolderJumper-3_P1.3mm_Bridged12_RoundedPad1.0x1.5mm
JP2: Jumper_3_Open; PinSocket_1x03_P2.54mm_Vertical
JP4: Jumper_2_Open; PinSocket_1x02_P2.54mm_Vertical
JP7: SolderJumper_2_Bridged; SolderJumper-2_P1.3mm_Bridged_RoundedPad1.0x1.5mm
JP9, JP10, JP11, JP12, JP13, JP14, JP15: SolderJumper_2_Open; SolderJumper-2_P1.3mm_Open_RoundedPad1.0x1.5mm
LOGO1: Logo_Open_Hardware_Large; OSHW-Logo2_14.6x12mm_SilkScreen
N1: G313; CASE_G313
R1, R2, R3, R9, R10, R11, R12, R19, R20, R21, R28, R29, R30, R31, R32, R33, R34: 330; R_0805_2012Metric
R4, R8: 10M; R_0805_2012Metric
R5: 1K5; R_0805_2012Metric
R6, R7: 22; R_0805_2012Metric
R13, R14, R27: 220; R_0805_2012Metric
R15, R16, R17, R23: 1K; R_0805_2012Metric
R18: 2K; R_0805_2012Metric
R22: 16K; R_0805_2012Metric
R24, R25: 560; R_0805_2012Metric
R26: 1k; R_0805_2012Metric
U1, U3: MCP23S17_SP; DIP-28_W7.62mm
U2: STM32F407VETx; LQFP-100_14x14mm_P0.5mm
U4: USBLC6-2SC6; SOT-23-6
U5: AMS1117; SOT-223-3_TabPin2
U6: 4N35; SMDIP-6_W7.62mm
U7, U8, U9, U10, U21: PC817; SMDIP-4_W7.62mm
U11, U12, U13, U14, U15, U16, U17, U18, U19, U20: IP4220CZ6; TSOP-6_1.65x3.05mm_P0.95mm
Y1: 32,768 кГц; Crystal_C26-LF_D2.1mm_L6.5mm_Horizontal_1EP_style2
Y2: 8MHz; Crystal_HC49-4H_Vertical

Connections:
3V: C6.1, C9.1, C11.1, C13.1, C14.1, C15.1, C16.1, C17.1, C18.1, C19.1, C20.1, C21.1, C22.1, C25.1, C27.1, C30.1, J6.1, J6.2, J16.1, J17.2, J18.3, J20.7, J20.9, J21.1, J22.3, J22.4, JP2.1, JP13.1, R1.2, R2.2, R3.2, R5.1, R9.2, R10.2, R11.2, R12.2, R27.2, R34.2, U1.9, U1.18, U2.11, U2.19, U2.21, U2.22, U2.28, U2.50, U2.75, U2.100, U3.9, U3.18, U5.2, U8.4, U9.4, U10.4, U11.5, U12.5, U13.5, U14.5, U15.5, U16.5, U17.5, U18.5, U19.5, U20.5
5V: C10.1, C12.1, J5.1, JP1.3, JP3.3, U4.5, U5.3
B1: J1.1, J2.2, U1.1, U12.4
B2: J1.2, J2.3, U1.2, U12.6
B3: J1.3, J2.4, U1.3, U12.3
B4: J1.4, J2.5, U1.4, U12.1
B5: J1.5, J2.6, U1.5, U17.4
B6: J1.6, J2.7, U1.6, U17.6
B7: J1.7, J3.2, U1.7, U17.3
B8: J1.8, J3.3, U1.8, U17.1
B9: J1.9, J3.4, U1.21, U15.4
B10: J1.10, J3.5, U1.22, U15.6
B11: J1.11, J3.6, U1.23, U15.3
B12: J1.12, J3.7, U1.24, U15.1
B13: J1.13, J4.2, U1.25, U13.4
B14: J1.14, J4.3, U1.26, U13.6
B15: J1.15, J4.4, U1.27, U13.3
B16: J1.16, J4.5, U1.28, U13.1
B17: J7.1, J8.2, U3.1, U19.1
B18: J7.2, J8.3, U3.2, U19.3
B19: J7.3, J8.4, U3.3, U19.6
B20: J7.4, J8.5, U3.4, U19.4
B21: J7.5, J8.6, U3.5, U20.4
B22: J7.6, J8.7, U3.6, U20.6
B23: J7.7, J9.2, U3.7, U20.3
B24: J7.8, J9.3, U3.8, U20.1
B25: J7.9, J9.4, U3.21, U16.4
B26: J7.10, J9.5, U3.22, U16.6
B27: J7.11, J9.6, U3.23, U16.3
B28: J7.12, J9.7, U3.24, U16.1
B29: J7.13, J10.2, U3.25, U14.4
B30: J7.14, J10.3, U3.26, U14.6
B31: J7.15, J10.4, U3.27, U14.3
B32: J7.16, J10.5, JP14.1, U3.28, U14.1
BOOT0: JP2.2, U2.94
BTN15: C3.1, R4.2, U2.8, Y1.1
BTN16: C4.1, R4.1, U2.9, Y1.2
COM: *D1.2, C23.2, C24.2, C26.2, C28.2, C29.2, D9.1, J11.2, J12.2, J13.1, J14.1, J14.19, J15.1, J15.10, JP8.1, R18.2, R25.2, U7.3, U21.3
CS: J22.16, U1.11, U2.51
DRIVE_ENABLE: *J1.1, J4.6, J10.6, J19.6, U21.2
DRIVE_PA+: J14.14, J15.20, R20.1
DRIVE_PA-: J14.12, J15.19, U9.2
DRIVE_PB+: J14.10, J15.18, R21.1
DRIVE_PB-: J14.8, J15.17, U10.2
DRIVE_PZ+: J14.4, J15.15, R19.1
DRIVE_PZ-: J14.6, J15.16, U8.2
DRIVE_SigIn1: J14.11, J15.6, U21.4
DRIVE_SigIn2: J14.13, J15.7, U7.4
DRIVE_VREF: C24.1, J13.4, J14.24, J15.25, JP7.2, R23.2
DRV_DIR: J22.29, R14.2, U2.42
DRV_PWM: J22.27, R13.2, U2.40
ENC_A: J22.12, JP5.1, JP6.3, U2.23
ENC_B: J22.11, JP5.3, JP6.1, U2.24
ENC_I: J22.14, R15.1, U2.25, U8.3
FORCE_LED_B: R29.2, R32.2, U2.62
FORCE_LED_G: R28.2, R33.2, U2.59
FORCE_LED_R: R30.2, R31.2, U2.61
GND: *J1.2, C1.2, C2.2, C3.2, C4.2, C5.2, C6.2, C7.1, C8.2, C9.2, C10.2, C11.2, C12.2, C13.2, C14.2, C15.2, C16.2, C17.2, C18.2, C19.2, C20.2, C21.2, C22.2, C25.2, C27.2, C30.2, D7.1, D11.1, D12.1, D13.1, J1.17, J1.18, J2.1, J3.1, J4.1, J5.4, J5.5, J6.4, J6.6, J6.8, J6.10, J6.12, J6.14, J6.16, J6.18, J6.20, J7.17, J7.18, J8.1, J9.1, J10.1, J16.2, J17.1, J18.2, J19.1, J20.6, J21.6, J22.1, J22.2, J22.5, J22.23, JP1.1, JP2.3, JP3.1, JP4.1, JP12.1, R15.2, R16.2, R17.2, U1.10, U1.15, U1.16, U1.17, U2.10, U2.20, U2.27, U2.74, U2.99, U3.10, U3.15, U3.16, U3.17, U4.2, U5.1, U6.2, U7.2, U11.2, U12.2, U13.2, U14.2, U15.2, U16.2, U17.2, U18.2, U19.2, U20.2, Y1.3
unnamed: C1.1, U2.49
unnamed: C2.1, U2.73
unnamed: C23.1, J13.3, JP7.1, R22.2, R23.1
unnamed: D1.1, J2.8
unnamed: D1.2, R1.1
unnamed: D2.1, J3.8
unnamed: D2.2, R2.1
unnamed: D3.1, J4.8
unnamed: D3.2, R3.1
unnamed: D4.1, J8.8
unnamed: D4.2, R9.1
unnamed: D5.1, J9.8
unnamed: D5.2, R10.1
unnamed: D6.1, J10.8
unnamed: D6.2, R11.1
unnamed: D7.2, R12.1
unnamed: D9.2, R26.2
unnamed: D10.1, J19.8
unnamed: D10.2, R34.1
unnamed: D11.2, R28.1
unnamed: D12.2, R29.1
unnamed: D13.2, R30.1
unnamed: J4.7, JP1.2
unnamed: J5.2, U4.3
unnamed: J5.3, U4.1
unnamed: J10.7, JP3.2
unnamed: J13.2, R18.1, R22.1, U6.4
unnamed: J14.25, J15.13, JP8.2
unnamed: J18.1, J21.9, JP12.2
unnamed: J19.2, R31.1
unnamed: J19.3, R32.1
unnamed: J19.4, R33.1
unnamed: J19.7, JP13.2
unnamed: J20.5, JP15.2
unnamed: JP5.2, R16.1, U9.3
unnamed: JP6.2, R17.1, U10.3
unnamed: JP8.3, R24.2, R25.1
unnamed: R5.2, R7.2, U4.4
unnamed: R6.2, U4.6
unnamed: R13.1, U6.1
unnamed: R14.1, U7.1
unnamed: R19.2, U8.1
unnamed: R20.2, U9.1
unnamed: R21.2, U10.1
unnamed: R27.1, U21.1
OSC_IN: C5.1, R8.2, U2.12, Y2.1
OSC_OUT: C8.1, R8.1, U2.13, Y2.2
PA13: J6.7, U2.72
PA14: J6.9, U2.76
PA15: J6.5, U2.77
PB3: J6.13, U2.89
PB4: J6.3, U2.90
PEDAL_BREAK: J18.5, J21.3, J22.21, U2.36, U18.6
PEDAL_CLUCH: J18.4, J21.4, J22.20, JP15.1, U2.33, U18.1
PEDAL_GAS: J18.6, J21.2, J22.22, U2.35, U18.4
PWR: *D1.1, C26.1, C28.1, C29.1, D8.1, J14.17, J15.2, J15.9, R24.1, R26.1, U6.5
PWR_IN: D8.2, J11.1, J12.1
RESET: C7.2, J6.15, J22.6, JP4.2, U2.14
SCK: J22.15, U1.12, U2.52
SHIFTER_X: J17.6, J20.4, J22.10, U2.17, U11.4
SHIFTER_Y: J17.7, J20.8, J22.7, U2.16, U18.3
SI: J22.17, U1.13, U2.54
SO: J22.18, U1.14, U2.53
SPI1_CS: J16.3, JP9.1, U2.29, U3.11
SPI1_CS_PROT: J17.5, J20.3, JP9.2, U11.6
SPI1_SCK: J16.4, JP11.1, U2.30, U3.12
SPI1_SCK_PROT: J17.3, J20.1, JP11.2, U11.3
SPI1_SI: J16.5, U2.32, U3.13
SPI1_SO: J16.6, JP10.1, U2.31, U3.14
SPI1_SO_PROT: J17.4, J20.2, JP10.2, JP14.2, U11.1
USB_DM: R6.1, U2.70
USB_DP: R7.1, U2.71

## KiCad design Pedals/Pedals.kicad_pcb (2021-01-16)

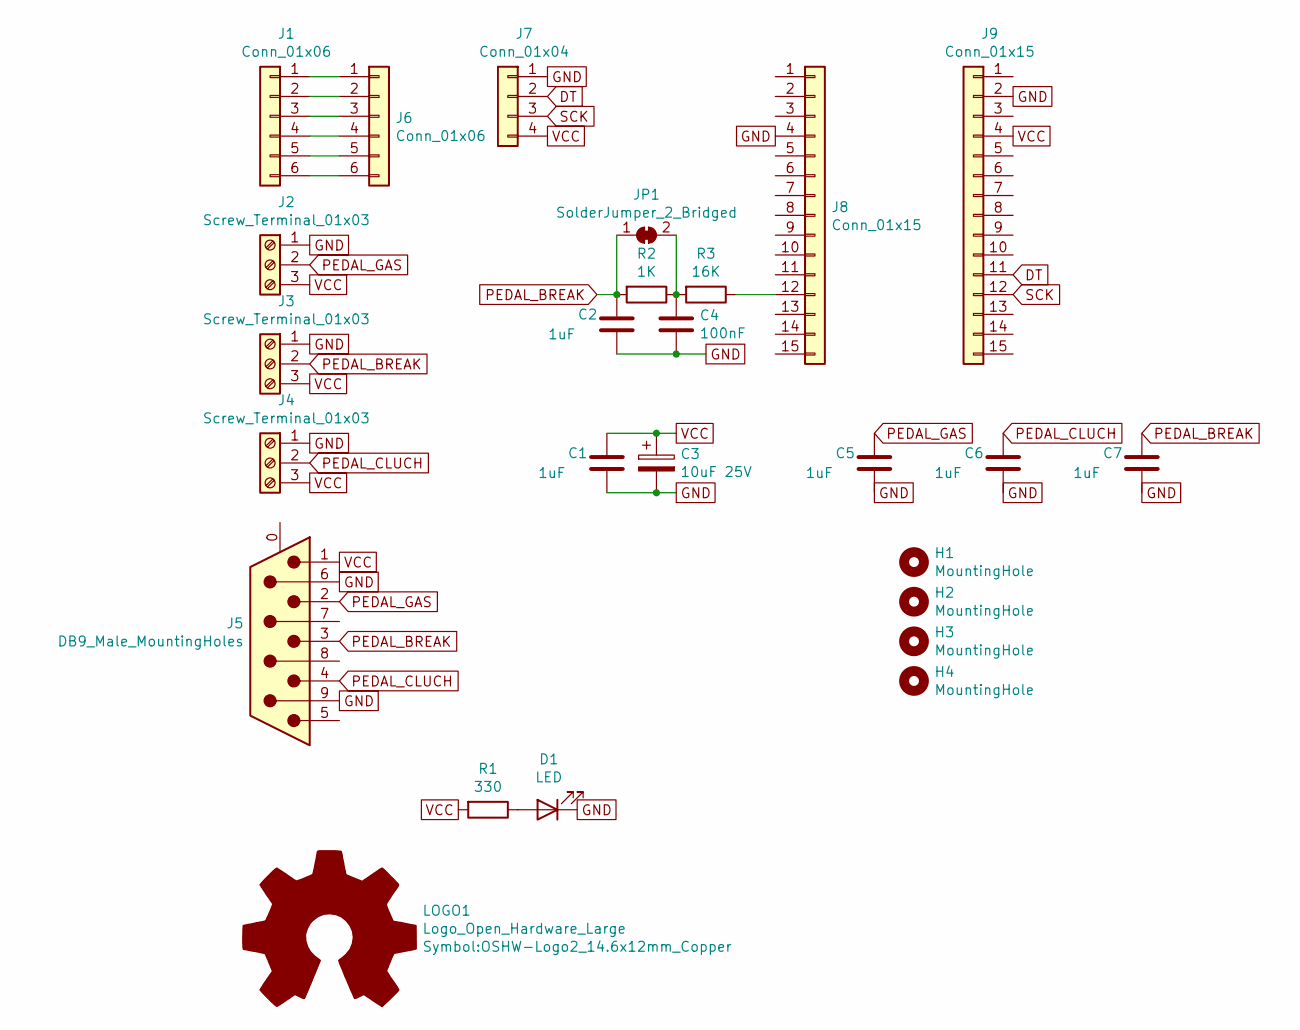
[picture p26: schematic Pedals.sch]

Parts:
C1, C2, C5, C6, C7: 1uF; C_0805_2012Metric
C3: 10uF 25V; CP_Elec_5x5.4
C4: 100nF; C_0805_2012Metric
D1: LED; LED_0805_2012Metric
H1, H2, H3, H4: MountingHole; MountingHole_2.5mm_Pad
J1: Conn_01x06; PinHeader_1x06_P2.54mm_Vertical
J2, J3, J4: Screw_Terminal_01x03; TerminalBlock_Phoenix_MKDS-1,5-3_1x03_P5.00mm_Horizontal
J5: DB9_Male_MountingHoles; DSUB-9_Male_Horizontal_P2.77x2.84mm_EdgePinOffset4.94mm_Hou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
J6: Conn_01x06; PinSocket_1x06_P2.54mm_Vertical
J7: Conn_01x04; PinSocket_1x04_P2.54mm_Vertical
J8, J9: Conn_01x15; PinSocket_1x15_P2.54mm_Vertical
JP1: SolderJumper_2_Bridged; SolderJumper-2_P1.3mm_Bridged_RoundedPad1.0x1.5mm
LOGO1: Logo_Open_Hardware_Large; OSHW-Logo2_14.6x12mm_Copper
R1: 330; R_0805_2012Metric
R2: 1K; R_0805_2012Metric
R3: 16K; R_0805_2012Metric

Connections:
DT: J7.2, J9.11
GND: C1.2, C2.2, C3.2, C4.2, C5.2, C6.2, C7.2, D1.1 (K), J2.1, J3.1, J4.1, J5.6, J5.9, J7.1, J8.4, J9.2
unnamed: C4.1, JP1.2 (B), R2.1, R3.2
unnamed: D1.2 (A), R1.1
unnamed: J1.1, J6.1
unnamed: J1.2, J6.2
unnamed: J1.3, J6.3
unnamed: J1.4, J6.4
unnamed: J1.5, J6.5
unnamed: J1.6, J6.6
unnamed: J8.12, R3.1
PEDAL_BREAK: C2.1, C7.1, J3.2, J5.3, JP1.1 (A), R2.2
PEDAL_CLUCH: C6.1, J4.2, J5.4
PEDAL_GAS: C5.1, J2.2, J5.2
SCK: J7.3, J9.12
VCC: C1.1, C3.1, J2.3, J3.3, J4.3, J5.1, J7.4, J9.4, R1.2

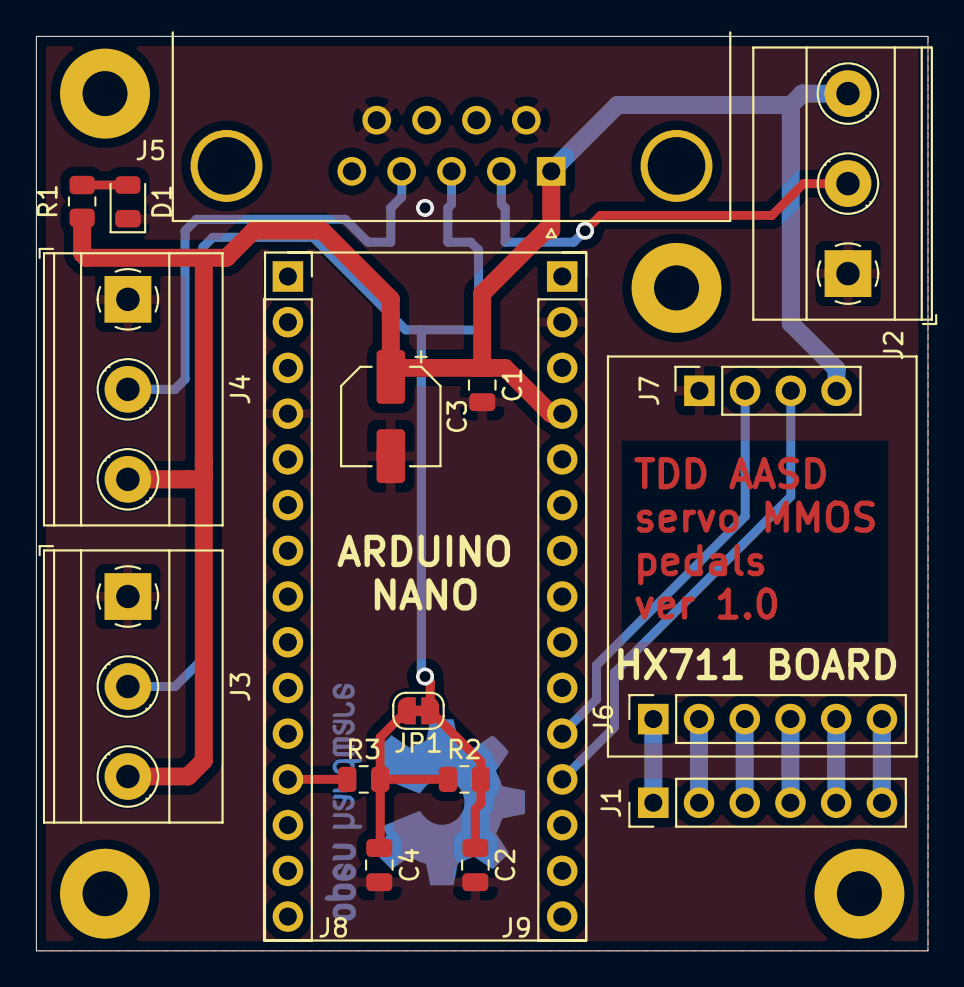
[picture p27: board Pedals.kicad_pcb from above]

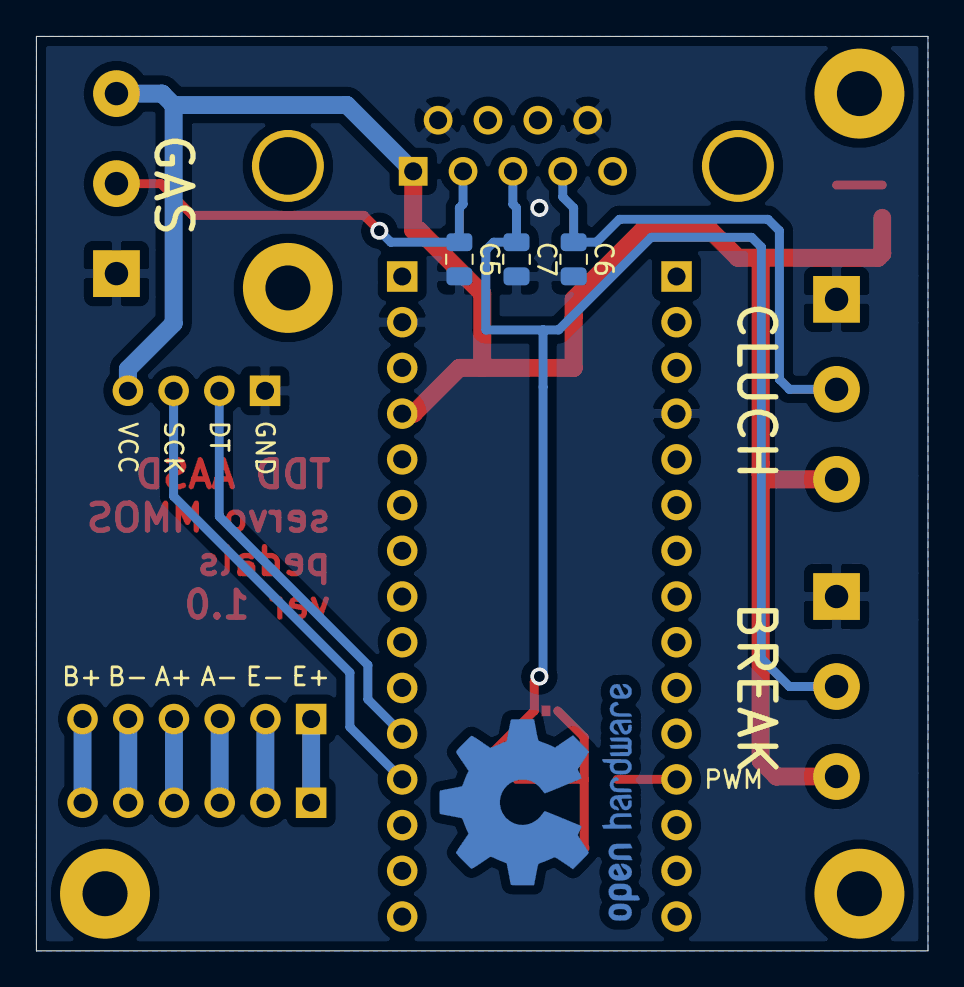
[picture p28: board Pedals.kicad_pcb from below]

Board: 2 copper layers, 49.5 x 50.8 mm, 26 parts (4 on the bottom side), 16 nets.

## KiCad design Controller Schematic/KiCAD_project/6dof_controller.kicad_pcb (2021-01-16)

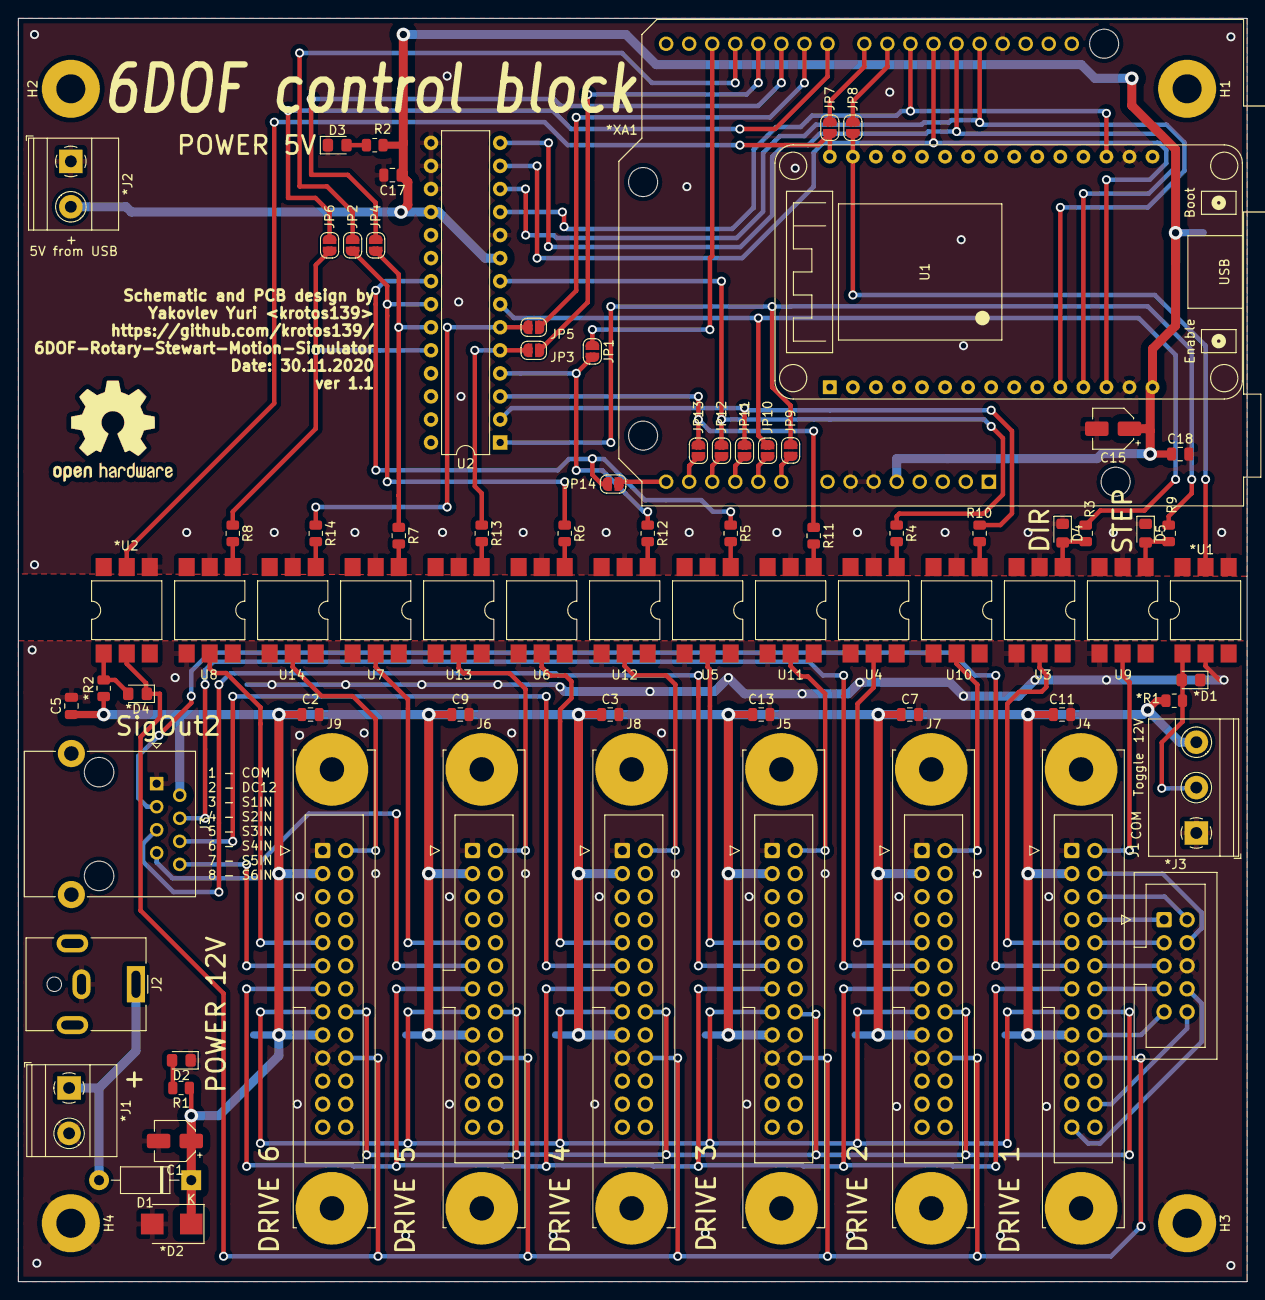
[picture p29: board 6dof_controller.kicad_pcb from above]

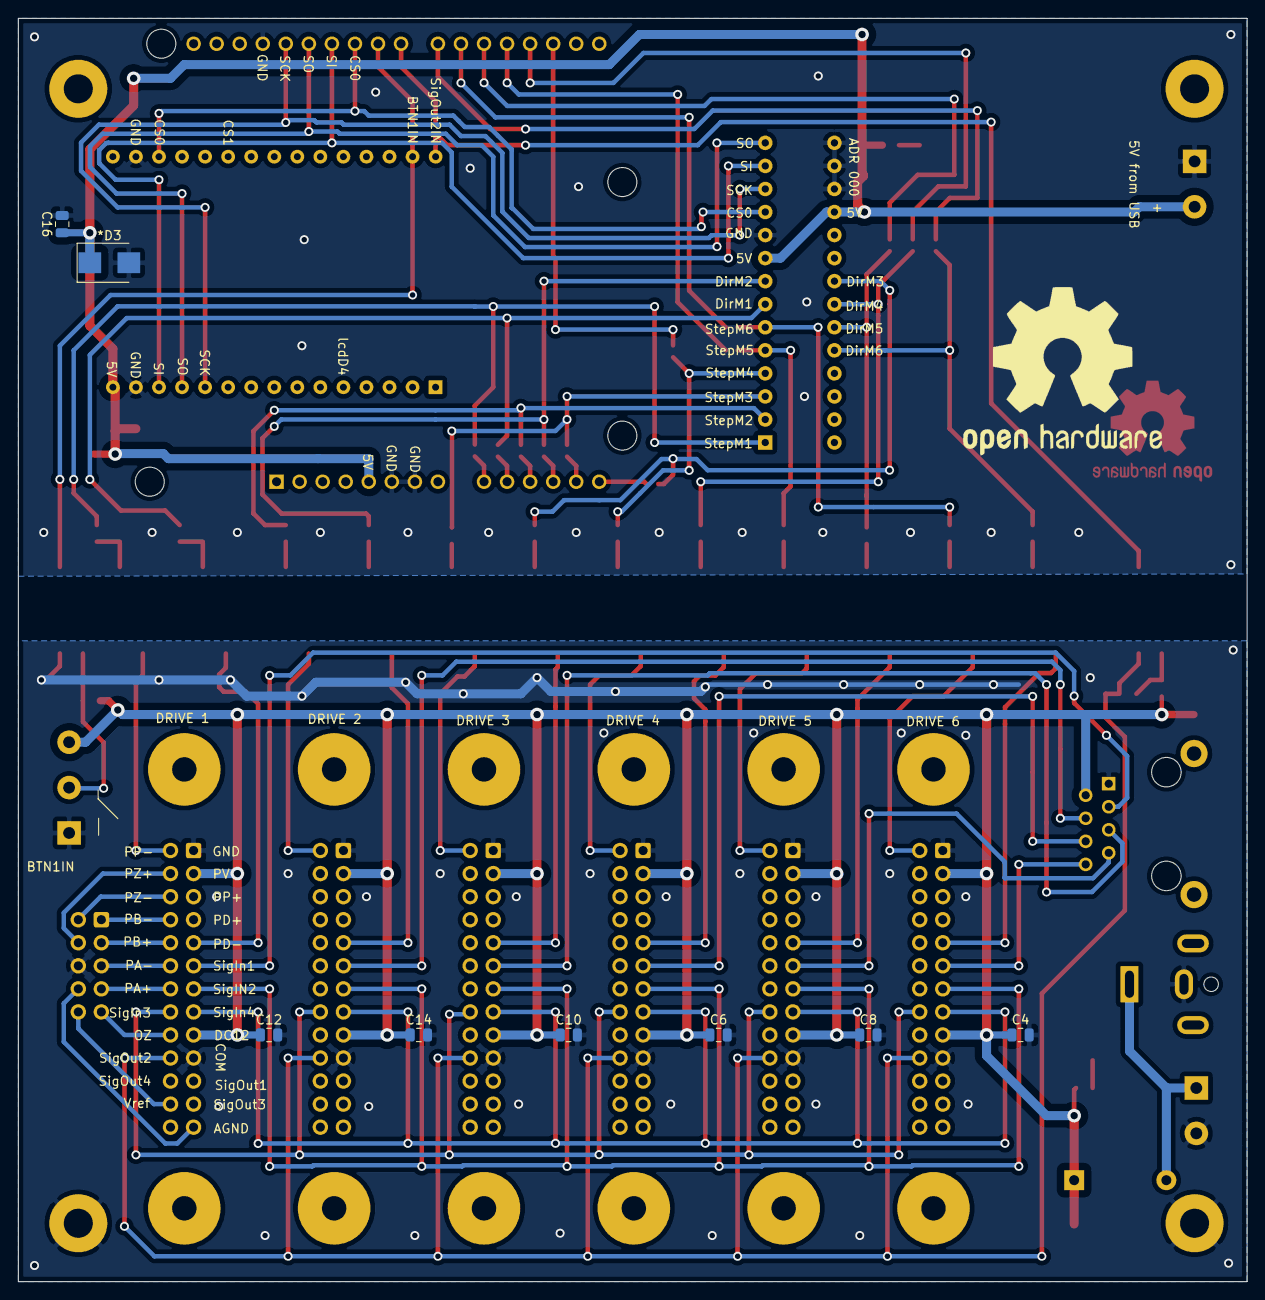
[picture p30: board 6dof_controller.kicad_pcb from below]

Board: 2 copper layers, 135.4 x 139.2 mm, 91 parts (8 on the bottom side), 84 nets.

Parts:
*D1, *D4: BL-LS0805UYC; LED_0805_2012Metric_Pad1.15x1.40mm_HandSolder
*D2, *D3: SM6T22A; D_SMB
*J1, *J2: Screw_Terminal_01x02; TerminalBlock_Phoenix_MKDS-1,5-2_1x02_P5.00mm_Horizontal
*J3: Conn_02x05_Top_Bottom; IDC-Header_2x05_P2.54mm_Vertical
*R1, *R2: 330; R_0805_2012Metric
*U1, *U2: 4N35; SMDIP-6_W9.53mm
*XA1: Arduino_Uno_Shield; Arduino_UNO_R3_WithMountingHoles
C1, C15: 1uF, 50V; CP_Elec_4x5.7
C2, C3, C4, C5, C6, C7, C8, C9, C10, C11, C12, C13, C14, C16, C17, C18: 0.1uF 50V; C_0805_2012Metric
D1: 1N4003; D_DO-41_SOD81_P10.16mm_Horizontal
D2, D3, D4, D5: BL-LS0805UYC; LED_0805_2012Metric_Pad1.15x1.40mm_HandSolder
H1, H2, H3, H4: MountingHole_Pad; MountingHole_3.2mm_M3_Pad
J1: Screw_Terminal_01x03; TerminalBlock_Phoenix_MKDS-1,5-3_1x03_P5.00mm_Horizontal
J2: DS-201; BarrelJack_CUI_PJ-063AH_Horizontal
J3: RJ45; RJ45_Ninigi_GE
J4, J5, J6, J7, J8, J9: Conn_02x13_Top_Bottom; IDC-Header_2x13-1MP_P2.54mm_Latch_Vertical
JP1, JP2, JP3, JP4, JP5, JP6, JP7, JP8, JP9, JP10, JP11, JP12, JP13, JP14: SolderJumper_2_Open; SolderJumper-2_P1.3mm_Open_RoundedPad1.0x1.5mm
LOGO1: Logo_Open_Hardware_Large; OSHW-Logo2_14.6x12mm_Copper
R1: 1K; R_0805_2012Metric
R2: 330; R_0805_2012Metric
R3, R4, R5, R6, R7, R8, R9, R10, R11, R12, R13, R14: 100; R_0805_2012Metric
U1: ESP32_DevKit_V1_DOIT; esp32_devkit_v1_doit
U2: MCP23SigIn1M17_SP; DIP-28_W7.62mm
U3, U4, U5, U6, U7, U8, U9, U10, U11, U12, U13, U14: 4N35; SMDIP-6_W9.53mm

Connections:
5V: *D3.1, *J2.2, *XA1.5, C15.1, C16.1, C17.1, C18.1, R2.1, U1.15, U2.9, U2.18
/DirM1: JP10.2, R3.1, U2.7
/DirM2: JP12.2, R4.1, U2.8
/DirM3: JP14.2, R5.1, U2.21
/DirM4: JP2.2, R6.1, U2.22
/DirM5: JP4.2, R7.1, U2.23
/DirM6: JP6.2, R8.1, U2.24
/StepM1: JP9.2, R9.1, U2.1
/StepM2: JP11.2, R10.1, U2.2
/StepM3: JP13.2, R11.1, U2.3
/StepM4: JP1.2, R12.1, U2.4
/StepM5: JP3.2, R13.1, U2.5
/StepM6: JP5.2, R14.1, U2.6
BTN1IN: *U1.5, JP8.2, U1.29
COM: *D1.1, *D2.2, *J1.2, *J3.6, *U1.2, C1.2, C2.2, C3.2, C4.2, C5.2, C6.2, C7.2, C8.2, C9.2, C10.2, C11.2, C12.2, C13.2, C14.2, D2.1, H3.1, H4.1, J1.1, J2.2, J3.1, J4.1, J4.19, J5.1, J5.19, J6.1, J6.19, J7.1, J7.19, J8.1, J8.19, J9.1, J9.19, U3.4, U4.4, U5.4, U6.4, U7.4, U8.4, U9.4, U10.4, U11.4, U12.4, U13.4, U14.4
CS0: *XA1.25, U1.18, U2.11
DC12: *D2.1, *R1.2, *R2.1, C1.1, C2.1, C3.1, C4.1, C5.1, C6.1, C7.1, C8.1, C9.1, C10.1, C11.1, C12.1, C13.1, C14.1, D1.1, J1.3, J3.2, J4.3, J4.17, J5.3, J5.17, J6.3, J6.17, J7.3, J7.17, J8.3, J8.17, J9.3, J9.17, R1.1
DM1: J4.9, U3.5
DM2: J7.9, U4.5
DM3: J5.9, U5.5
DM4: J8.9, U6.5
DM5: J6.9, U7.5
DM6: J9.9, U8.5
Earth_Protective: *D3.2, *J2.1, *U1.4, *U2.4, *XA1.6, *XA1.7, *XA1.29, C15.2, C16.2, C17.2, C18.2, D3.1, D4.1, D5.1, U1.14, U1.17, U2.10, U2.15, U2.16, U2.17, U3.2, U4.2, U5.2, U6.2, U7.2, U8.2, U9.2, U10.2, U11.2, U12.2, U13.2, U14.2
unnamed: *D1.2, *R1.1, *U1.1, J1.2
unnamed: *D4.2, *R2.2, *U2.1
unnamed: *J1.1, D1.2, J2.1
unnamed: *J3.1, J4.8
unnamed: *J3.2, J4.6
unnamed: *J3.3, J4.10
unnamed: *J3.4, J4.4
unnamed: *J3.5, J4.12
unnamed: *J3.7, J4.14
unnamed: *J3.8, J4.25
unnamed: *J3.9, J4.18
unnamed: *J3.10, J4.24
unnamed: *XA1.9, JP9.1
unnamed: *XA1.10, JP10.1
unnamed: *XA1.11, JP11.1
unnamed: *XA1.12, JP12.1
unnamed: *XA1.13, JP13.1
unnamed: *XA1.14, JP14.1
unnamed: *XA1.17, JP1.1
unnamed: *XA1.18, JP2.1
unnamed: *XA1.19, JP3.1
unnamed: *XA1.20, JP4.1
unnamed: *XA1.21, JP5.1
unnamed: *XA1.22, JP6.1
unnamed: *XA1.23, JP7.1
unnamed: *XA1.24, JP8.1
unnamed: D2.2, R1.2
unnamed: D3.2, R2.2
unnamed: D4.2, R3.2, U3.1
unnamed: D5.2, R9.2, U9.1
unnamed: R4.2, U4.1
unnamed: R5.2, U5.1
unnamed: R6.2, U6.1
unnamed: R7.2, U7.1
unnamed: R8.2, U8.1
unnamed: R10.2, U10.1
unnamed: R11.2, U11.1
unnamed: R12.2, U12.1
unnamed: R13.2, U13.1
unnamed: R14.2, U14.1
SCK: *XA1.28, U1.11, U2.12
SI: *XA1.26, U1.13, U2.13
SM1: J4.2, U9.5
SM2: J7.2, U10.5
SM3: J5.2, U11.5
SM4: J8.2, U12.5
SM5: J6.2, U13.5
SM6: J9.2, U14.5
SO: *XA1.27, U1.12, U2.14
SigIn1M1: J3.3, J4.11
SigIn1M2: J3.4, J7.11
SigIn1M3: J3.5, J5.11
SigIn1M4: J3.6, J8.11
SigIn1M5: J3.7, J6.11
SigIn1M6: J3.8, J9.11
SigIn2: J4.13, J5.13, J6.13, J7.13, J8.13, J9.13
SigIn3: J4.16, J5.16, J6.16, J7.16, J8.16, J9.16
SigIn4: J4.15, J5.15, J6.15, J7.15, J8.15, J9.15
SigOut2: *D4.1, *U2.2, J4.20, J5.20, J6.20, J7.20, J8.20, J9.20
SigOut2IN: *U2.5, JP7.2, U1.30

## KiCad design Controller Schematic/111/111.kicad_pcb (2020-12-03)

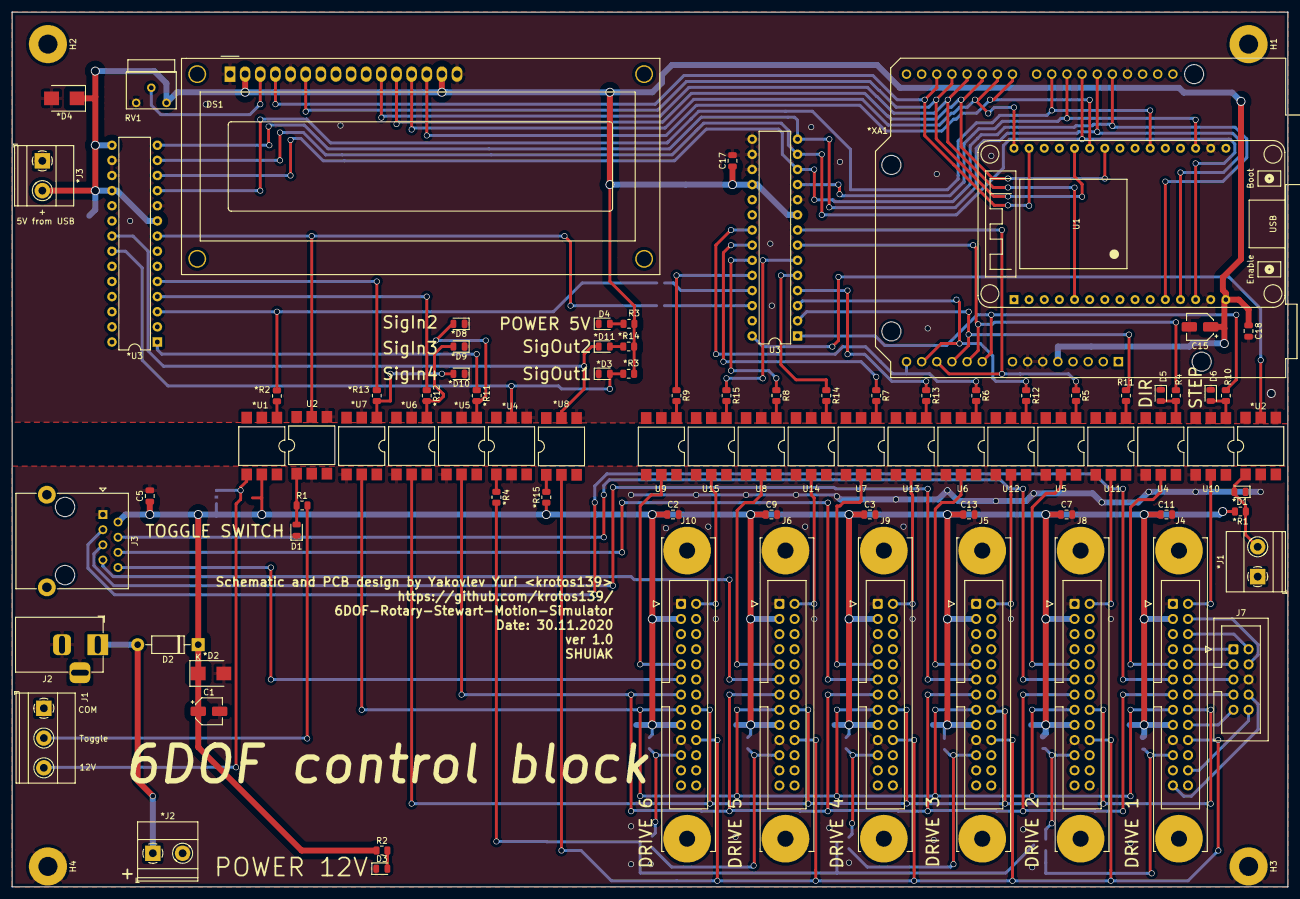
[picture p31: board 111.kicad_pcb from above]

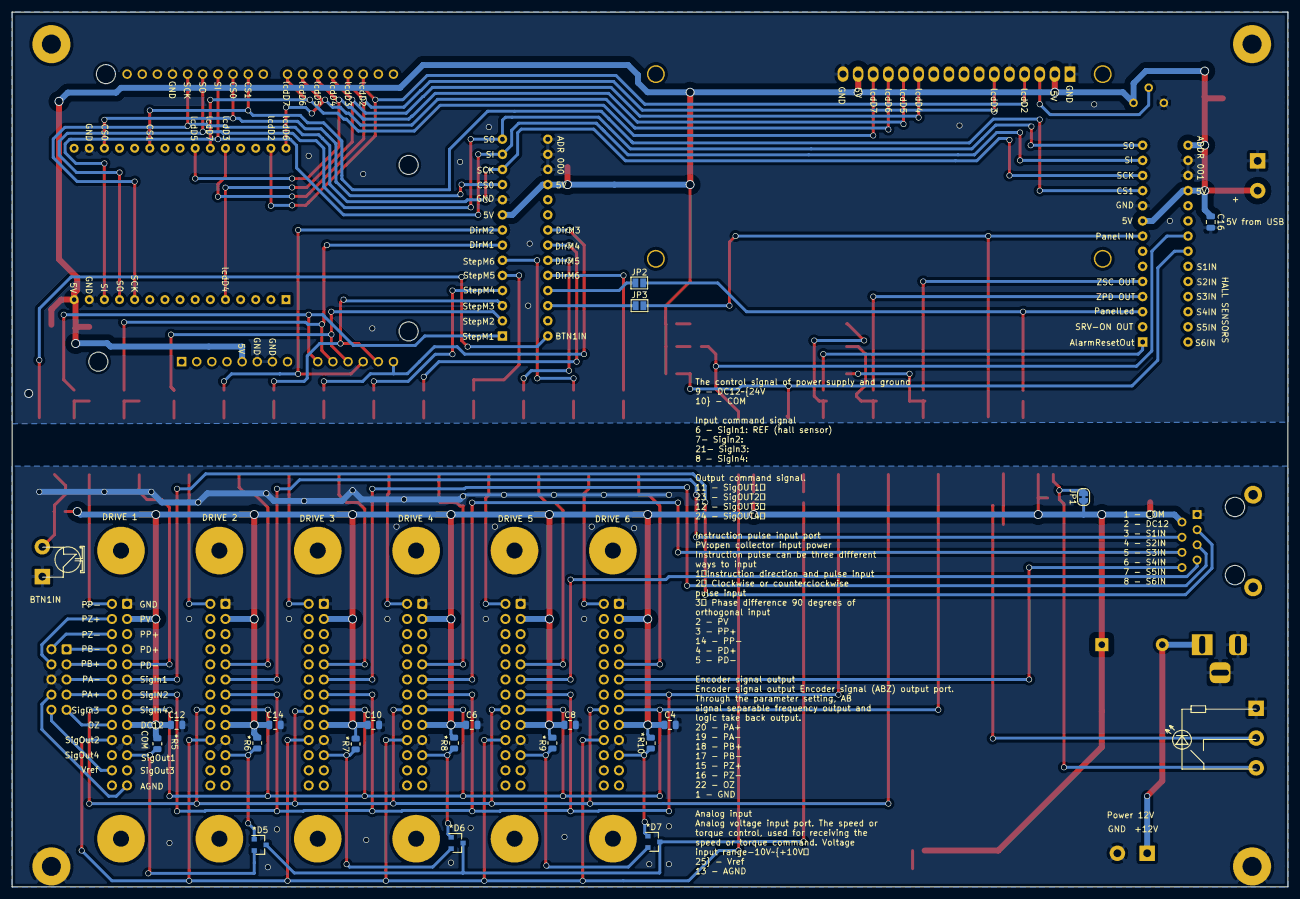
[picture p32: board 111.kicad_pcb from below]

Board: 2 copper layers, 214.1 x 146.8 mm, 111 parts (19 on the bottom side), 102 nets.

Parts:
*D1, *D3, *D8, *D9, *D10, *D11: BL-LS0805UYC; LED_0805_2012Metric
*D2, *D4: SM6T22A; D_SMB
*D5, *D6, *D7: BAV23; SOT-23
*J1, *J2, *J3: Screw_Terminal_01x02; TerminalBlock_Phoenix_MKDS-1,5-2_1x02_P5.00mm_Horizontal
*R1, *R3, *R4, *R5, *R6, *R7, *R8, *R9, *R10, *R14, *R15: 330; R_0805_2012Metric
*R2, *R11, *R12, *R13: 100; R_0805_2012Metric
*U1, *U2, *U4, *U5, *U6, *U7, *U8: 4N35; SMDIP-6_W9.53mm
*U3: MCP23SigIn1M17_SP; DIP-28_W7.62mm
*XA1: Arduino_Uno_Shield; Arduino_UNO_R3_WithMountingHoles
C1, C15: 1uF, 50V; CP_Elec_4x5.7
C2, C3, C4, C5, C6, C7, C8, C9, C10, C11, C12, C13, C14, C16, C17, C18: 0.1uF 50V; C_0805_2012Metric
D1, D3, D4, D5, D6: BL-LS0805UYC; LED_0805_2012Metric
D2: 1N4003; D_DO-41_SOD81_P10.16mm_Horizontal
DS1: WC1602A
H1, H2, H3, H4: MountingHole_Pad; MountingHole_3.2mm_M3_Pad
J1: Screw_Terminal_01x03; TerminalBlock_Phoenix_MKDS-1,5-3_1x03_P5.00mm_Horizontal
J2: DS-201; BarrelJack_Horizontal
J3: RJ45; RJ45_Ninigi_GE
J4, J5, J6, J8, J9, J10: Conn_02x13_Top_Bottom; IDC-Header_2x13-1MP_P2.54mm_Latch_Vertical
J7: Conn_02x05_Top_Bottom; IDC-Header_2x05_P2.54mm_Vertical
JP1: SolderJumper_2_Bridged; SolderJumper-2_P1.3mm_Bridged_RoundedPad1.0x1.5mm
JP2, JP3: SolderJumper_2_Open; SolderJumper-2_P1.3mm_Open_Pad1.0x1.5mm
R1, R2, R3: 330; R_0805_2012Metric
R4, R5, R6, R7, R8, R9, R10, R11, R12, R13, R14, R15: 100; R_0805_2012Metric
RV1: R_POT; Potentiometer_Bourns_3339W_Horizontal
U1: ESP32_DevKit_V1_DOIT; esp32_devkit_v1_doit
U2, U4, U5, U6, U7, U8, U9, U10, U11, U12, U13, U14, U15: 4N35; SMDIP-6_W9.53mm
U3: MCP23SigIn1M17_SP; DIP-28_W7.62mm

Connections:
5V: *D4.1, *J3.2, *R3.1, *R14.1, *U3.9, *U3.15, *U3.18, *XA1.5, C15.1, C16.1, C17.1, C18.1, DS1.2, DS1.15, R3.1, RV1.3, U1.15, U3.9, U3.18
#SigIn2: *R11.1, *U3.1
#SigIn3: *R12.1, *U3.3
#SigIn4: *R13.1, *U3.4
/DirM1: *XA1.10, R4.1, U3.7
/DirM2: *XA1.12, R5.1, U3.8
/DirM3: *XA1.14, R6.1, U3.21
/DirM4: R7.1, U3.22
/DirM5: R8.1, U3.23
/DirM6: R9.1, U3.24
/StepM1: *XA1.9, R10.1, U3.1
/StepM2: *XA1.11, R11.1, U3.2
/StepM3: *XA1.13, R12.1, U3.3
/StepM4: R13.1, U3.4
/StepM5: R14.1, U3.5
/StepM6: R15.1, U3.6
BTN1IN: *U2.5, U3.28
COM: *D1.1, *D2.2, *J1.1, *J2.2, *U2.2, *U4.2, *U5.4, *U6.4, *U7.4, C1.2, C2.2, C3.2, C4.2, C5.2, C6.2, C7.2, C8.2, C9.2, C10.2, C11.2, C12.2, C13.2, C14.2, D1.1, D3.1, H3.1, H4.1, J1.1, J2.2, J2.3, J3.1, J4.1, J4.19, J5.1, J5.19, J6.1, J6.19, J7.6, J8.1, J8.19, J9.1, J9.19, J10.1, J10.19, U2.2, U4.4, U5.4, U6.4, U7.4, U8.4, U9.4, U10.4, U11.4, U12.4, U13.4, U14.4, U15.4
CS0: *XA1.25, U1.18, U3.11
CSigIn1M1: *U3.11, *XA1.24, U1.21
DC12: *D2.1, *R1.2, *R5.2, *R6.2, *R7.2, *R8.2, *R9.2, *R10.2, *R15.1, *U1.5, C1.1, C2.1, C3.1, C4.1, C5.1, C6.1, C7.1, C8.1, C9.1, C10.1, C11.1, C12.1, C13.1, C14.1, D2.1, J3.2, J4.3, J4.17, J5.3, J5.17, J6.3, J6.17, J8.3, J8.17, J9.3, J9.17, J10.3, J10.17, JP1.1, R2.1
DM1: J4.9, U4.5
DM2: J8.9, U5.5
DM3: J5.9, U6.5
DM4: J9.9, U7.5
DM5: J6.9, U8.5
DM6: J10.9, U9.5
Earth_Protective: *D3.1, *D4.2, *D8.1, *D9.1, *D10.1, *J3.1, *U1.2, *U2.4, *U3.10, *U3.16, *U3.17, *U4.4, *U5.2, *U6.2, *U7.2, *U8.4, *XA1.6, *XA1.7, *XA1.29, C15.2, C16.2, C17.2, C18.2, D4.1, D5.1, D6.1, DS1.1, DS1.5, DS1.16, RV1.1, U1.14, U1.17, U2.4, U3.10, U3.15, U3.16, U3.17, U4.2, U5.2, U6.2, U7.2, U8.2, U9.2, U10.2, U11.2, U12.2, U13.2, U14.2, U15.2
LCDD2: *XA1.17, DS1.4, U1.29
LCDD3: *XA1.18, DS1.6, U1.26
LCDD4: *XA1.19, DS1.11, U1.5
LCDD5: *XA1.20, DS1.12, U1.24
LCDD6: *XA1.21, DS1.13, U1.30
LCDD7: *XA1.22, DS1.14, U1.25
unnamed: *D1.2, *J1.2, *R1.1, *U2.1
unnamed: *D5.3, *D6.3, *D7.3, *R4.2
unnamed: *D8.2, *R11.2, *U5.1
unnamed: *D9.2, *R12.2, *U6.1
unnamed: *D10.2, *R13.2, *U7.1
unnamed: *D11.2, *R14.2
unnamed: *J2.1, D2.2, J2.1
unnamed: *R2.1, *U1.1
unnamed: *R4.1, *U4.1
unnamed: *R15.2, *U8.1
unnamed: *U1.4, J1.3, JP1.2
unnamed: D1.2, R1.1, U2.1
unnamed: D3.2, R2.2
unnamed: D4.2, R3.2
unnamed: D5.2, R4.2, U4.1
unnamed: D6.2, R10.2, U10.1
unnamed: DS1.3, RV1.2
unnamed: J1.2, R1.2
unnamed: J4.4, J7.4
unnamed: J4.6, J7.2
unnamed: J4.8, J7.1
unnamed: J4.10, J7.3
unnamed: J4.12, J7.5
unnamed: J4.14, J7.7
unnamed: J4.18, J7.9
unnamed: J4.24, J7.10
unnamed: J4.25, J7.8
unnamed: JP2.1, U3.25
unnamed: JP3.1, U3.26
unnamed: R5.2, U5.1
unnamed: R6.2, U6.1
unnamed: R7.2, U7.1
unnamed: R8.2, U8.1
unnamed: R9.2, U9.1
unnamed: R11.2, U11.1
unnamed: R12.2, U12.1
unnamed: R13.2, U13.1
unnamed: R14.2, U14.1
unnamed: R15.2, U15.1
NotSigOut1IN: *D3.2, *R3.2, *U3.22, *U4.5
PanelIN: *U3.8, JP3.2, U2.5
PanelLED: *R2.2, *U3.5, JP2.2
SCK: *U3.12, *XA1.28, U1.11, U3.12
SI: *U3.13, *XA1.26, U1.13, U3.13
SM1: J4.2, U10.5
SM2: J8.2, U11.5
SM3: J5.2, U12.5
SM4: J9.2, U13.5
SM5: J6.2, U14.5
SM6: J10.2, U15.5
SO: *U3.14, *XA1.27, U1.12, U3.14
SigIn1M1: J3.3, J4.11
SigIn1M2: J3.4, J8.11
SigIn1M3: J3.5, J5.11
SigIn1M4: J3.6, J9.11
SigIn1M5: J3.7, J6.11
SigIn1M6: J3.8, J10.11
SigIn2: *U5.5, J4.13, J5.13, J6.13, J8.13, J9.13, J10.13
SigIn3: *U6.5, J4.16, J5.16, J6.16, J8.16, J9.16, J10.16
SigIn4: *U7.5, J4.15, J5.15, J6.15, J8.15, J9.15, J10.15
SigOut1M1: *D5.2, *R5.1, J4.21
SigOut1M2: *D5.1, *R6.1, J8.21
SigOut1M3: *D6.2, *R7.1, J5.21
SigOut1M4: *D6.1, *R8.1, J9.21
SigOut1M5: *D7.2, *R9.1, J6.21
SigOut1M6: *D7.1, *R10.1, J10.21
SigOut2: *U8.2, J4.20, J5.20, J6.20, J8.20, J9.20, J10.20
SigOut2IN: *D11.1, *U3.21, *U8.5

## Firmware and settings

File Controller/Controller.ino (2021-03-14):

#include <sstream>
#include <Preferences.h>
#include "Bounce2.h"
#include <BLEDevice.h>
#include <BLEUtils.h>
#include <BLEServer.h>  
#include <Wire.h>
#include <SPI.h>
#include "MCP23S17.h"
#include <EEPROM.h>
#include "soc/timer_group_struct.h"
#include "soc/timer_group_reg.h"
#include <BLE2902.h>
#include <cstring>
#include "freertos/FreeRTOS.h"
#include "freertos/timers.h"
#include "DigitalFilters.h"
#include "helpers.h"

using namespace std;

//Filter test
constexpr float dtUsed = 0.001;//time between incoming PC packet used in filter calc
std::vector<LowPassFilter> lpfVec;

//uncomment this to slow down motor rate so you can visually see the incrementing of the motor positions in real time. 
//#define DEBUG_MOTORS 1

//when bench testing the esp32, and have no estop connected to PCB, uncomment to allow system to activate motors anyway.
#define DEBUG_NO_ESTOP 1

//for saving of filter parameters
Preferences preferences;
int microInterval = MICRO_INTERVAL_FAST;

BLEServer* pServer = NULL;
BLECharacteristic* pPostionCharacteristic = NULL;
bool deviceConnected = false;
bool oldDeviceConnected = false;
uint32_t value = 0;

//Debouncer for Estop/Pause button
Bounce debouncedEStop = Bounce(); 

//pin number for step and direction pins on the MCP23S17
const int stepPins[] = {8,9,10,11,12,13};   
const int dirPins[] = {14,15,0,1,2,3};

//Lock to protect the Motor position array
SemaphoreHandle_t xMutex;

//CPU tasks, all GPIO for motors is on 2nd CPU, this frees main CPU to process position data and talk to PC and BLE client
TaskHandle_t InterfaceMonitorTask;
TaskHandle_t GPIOLoopTask;
TimerHandle_t wtmr;

//multiplexers for communicating with all 6 servo controllers. 
SPIClass hspi( HSPI );
MCP23S17 outputBank( &hspi, 15, 0 );

//soft estop,  this will prevent changes of position from pc to be applied.
//you should have a power kill near by as well,
volatile bool isPausedEStop = false;
volatile bool isRateLimiting = false;

//max angle to allow the platform arms travel in degrees ie +-60 degrees. 
const float servo_min=radians(-60),servo_max=radians(60);

//time helper for creating individual pulses for motors
int64_t currentMicros = esp_timer_get_time();
int64_t  previousMicros = 0;

//time helpers for creating Ble outputs
int64_t currentMicrosBle = esp_timer_get_time();
int64_t  previousMicrosBle = 0;

//this should be refactored out?
static long servo_pos[6];

//Access to each of the 6 ac motor current status.
volatile struct acServo motors[6];

//helper for pulses sent to GPIO, when false, means that the next pulse will be logical 0. 
boolean pinState = false;

//buffers for GPIO state, each motor pulse state dir / position, is loaded into these. 
//two are used to stagger output, for you need to set direction slightly prior to setting position change.
uint16_t motorStepDirValue = 0;   
uint16_t motorStepDirValue2 = 0;   

//current target from pc, modified from 2 seperate tasks/cores
static volatile float arr[6]={0,0,0, 0,0,0};

void setPos(){  
  
    //Platform and Base Coords
    for(int i = 0; i < 6; i++)
    {    
        long x = 0;
        float alpha = getAlpha(i,arr);

        if(alpha >= servo_min && alpha <= servo_max)
        {
            //this takes the Radian angle, and scales that value to pulse position.
            //This is calibrated to the real world. with a 50:1 gear, and instructed to move +-60 degrees and finding a servoPulseMultiplierPerRadian that makes that happen.
            if(i==INV1||i==INV2||i==INV3){
                x = -(alpha)*servoPulseMultiplierPerRadian;
            }
            else{
                x = (alpha)*servoPulseMultiplierPerRadian;
            }
    
            servo_pos[i] = x;            
        }     
    }

    //lock access to motor array
    xSemaphoreTake( xMutex, portMAX_DELAY );
    
    for(int i = 0; i < 6; i++)
    {
        motors[i].targetpos = servo_pos[i];
    }   
    
    //give up lock
    xSemaphoreGive( xMutex );     
}

//parses the data packet from the pc => x,y,z,Ry,Rx,RZ
void process_data ( char * data)
{ 
    int i = 0; 
    char *tok = strtok(data, ",");
    
    float arrRaw[]={0,0,0,0,0,0};
    float arrRateLimited[]={0,0,0,0,0,0};
    
    while (tok != NULL) {
      double value = (float)atof(tok);
      float temp = 0.0;
      
      //these are tuned to my specific platform,.. to ensure a value does not get to high and break something  
      //todo, make this dynamic and locked in from the android app
      if(i == 2)
        temp =mapfloat(value, 0, 4094, -7, 7);//hieve 
      else if(i > 2)//rotations, pitch,roll,yaw
        temp = mapfloat(value, 0, 4094, -30, 30) *(pi/180.0);
      else//sway,surge
        temp = mapfloat(value, 0, 4094, -8, 8); 

        arrRaw[i++] = temp;
      
        tok = strtok(NULL, ",");
    }   
      
  //filter 
  //TODo make this a function call, add ability to stack filters?
  //Apply filter to raw PC Data
  //for(int i=0;i<6;i++)
  //{
  //  arrTemp[i] = lpfVec[i].update(arrTemp[i]);
  //}

  //if we are not in an estop pause, allow setting of the current position
  if(!isPausedEStop)
  {
    //if we are just after resetting estop, we will be in a ratelimited mode until the ratelimited position is within close proximity of the actual last stored location.
    if(isRateLimiting)
    {    
        bool isNotWithinLimit = false;
        for(int i=0;i<6;i++)
        {
          arrRateLimited[i] = rateLimit(arrRaw[i],arr[i]);
        
          //close proximity detector, if we are within tolerance, we will set a flag so we break out of the rate limited mode
          float diff = arr[i] - arrRaw[i];
          if (diff > .1 || diff < -.1) {
            isNotWithinLimit = true;
          }  
        }

        //when all are within tolerance, flip ratelimit... rider Go Fast now...
        if(!isNotWithinLimit)
        {
          isRateLimiting = false;
        }

        for(int i=0;i<6;i++)
        {
          arr[i] = arrRateLimited[i];
        }
    }
    else
    {
        for(int i=0;i<6;i++)
        {
          arr[i] = arrRaw[i];
        }
    }

    //Computes the next position of each of the arms based on the values sent.
    setPos();
  }
    
} 

//reset timer
void ping( TimerHandle_t xTimer )
{ 
    //Resets the watchdog timer in the ESP32/rtos
    //this is needed in order not have the thing reset every few seconds.
    TIMERG0.wdt_wprotect=TIMG_WDT_WKEY_VALUE;
    TIMERG0.wdt_feed=1;
    TIMERG0.wdt_wprotect=0;

    //Restart timer for this method
    xTimerStart(wtmr, 0);
}

//to pause platform, send "1", to start send "0" string
class BlePauseCallback: public BLECharacteristicCallbacks {

    void onWrite(BLECharacteristic *pCharacteristic) {
   
      string result = pCharacteristic->getValue().c_str();
      
      Serial.println("BlePauseCallback");
      Serial.println(pCharacteristic->getValue().c_str());
    
      int i = atoi(pCharacteristic->getValue().c_str());
    
      if(i == 0)
      {  
        pauseEStop();
      }
      else if(i == 1)
      {
        resumeEStop();
      }
    }    
};

//Filter saving from Ble, expecting array of Doubles, 0-100 for each axis comma delimeted.
//i.e. 14.2,16.3,55.6,54.3,34.9
class BleFilterCallback: public BLECharacteristicCallbacks {

    //read filter parameters into Android App
    void onRead(BLECharacteristic *pCharacteristic) {
            
      std::ostringstream os;
      os << getAxis1Filter() << "," << getAxis2Filter() << "," << getAxis3Filter() << "," << getAxis4Filter() << "," << getAxis5Filter() << "," << getAxis6Filter();
  
      pCharacteristic->setValue(os.str());
    }

    //Android app sent new parameters, lets save them to eeprom and reload current filter
    void onWrite(BLECharacteristic *pCharacteristic) {
      
      std::string value = pCharacteristic->getValue();
      Serial.println("Filter settings BLE");
      Serial.println(value.c_str());
      if (value.length() > 0) {
          int arr[6]={0,0,0, 0,0,0};
          int i = 0; 
          char *tok;
          char *rawTokens = new char[value.size()+1];
          strcpy(rawTokens, value.c_str());
       
          tok = strtok(rawTokens, ",");
      
          while (tok != NULL) {
              int value = (int)atoi(tok);
                arr[i++] = value;
                tok = strtok(NULL, ",");
          }   
          
          Serial.println("Save");
          Serial.print("Axis 1: ");
          Serial.println(arr[0]);
          Serial.print("Axis 2: ");
          Serial.println(arr[1]);
          Serial.print("Axis 3: ");
          Serial.println(arr[2]);
          Serial.print("Axis 4: ");
          Serial.println(arr[3]);
          Serial.print("Axis 5: ");
          Serial.println(arr[4]);
          Serial.print("Axis 6: ");
          Serial.println(arr[5]);

          setAxis1(arr[0]);
          setAxis2(arr[1]);
          setAxis3(arr[2]);
          setAxis4(arr[3]);
          setAxis5(arr[4]);
          setAxis6(arr[5]);

          //After saving to EEPROM, load to current running filter
          loadFilterAxis();
      }
    }
};

//loads the EEPROM values for each axis
void loadFilterAxis(){

  Serial.println("Load");
  Serial.print("Axis 1: ");
  Serial.println(getAxis1Filter());
  Serial.print("Axis 2: ");
  Serial.println(getAxis2Filter());
  Serial.print("Axis 3: ");
  Serial.println(getAxis3Filter());
  Serial.print("Axis 4: ");
  Serial.println(getAxis4Filter());
  Serial.print("Axis 5: ");
  Serial.println(getAxis5Filter());
  Serial.print("Axis 6: ");
  Serial.println(getAxis6Filter());
  
  LowPassFilter lpf1(dtUsed, 2 * M_PI * getAxis1Filter());
  LowPassFilter lpf2(dtUsed, 2 * M_PI * getAxis2Filter());
  LowPassFilter lpf3(dtUsed, 2 * M_PI * getAxis3Filter());
  LowPassFilter lpf4(dtUsed, 2 * M_PI * getAxis4Filter());
  LowPassFilter lpf5(dtUsed, 2 * M_PI * getAxis5Filter());
  LowPassFilter lpf6(dtUsed, 2 * M_PI * getAxis6Filter());
  
  lpfVec.clear();
  lpfVec.push_back(lpf1);
  lpfVec.push_back(lpf2);
  lpfVec.push_back(lpf3);
  lpfVec.push_back(lpf4);
  lpfVec.push_back(lpf5);
  lpfVec.push_back(lpf6);
  
  Serial.print("lpfVec vector loaded");
}

class ServerCallbacks: public BLEServerCallbacks {
    void onConnect(BLEServer* pServer) {
      deviceConnected = true;
    };

    void onDisconnect(BLEServer* pServer) {
      deviceConnected = false;
    }
};

//setup BLE access notify service and configuration characteristics 
void setupBle(){
  
  Serial.println("Starting BLE init!");

  BLEDevice::init("Open 6DOF");
  BLEServer *pServer = BLEDevice::createServer();
  pServer->setCallbacks(new ServerCallbacks());
  BLEService *pService = pServer->createService(SERVICE_UUID);
  
  BLECharacteristic *pPauseCharacteristic = pService->createCharacteristic(
                                         PAUSECHARACTERISTIC_UUID,
                                         BLECharacteristic::PROPERTY_READ |
                                         BLECharacteristic::PROPERTY_WRITE
                                       );

  BLECharacteristic *pFilterCharacteristic = pService->createCharacteristic(
                                         FILTERCHARACTERISTIC_UUID,
                                         BLECharacteristic::PROPERTY_READ |
                                         BLECharacteristic::PROPERTY_WRITE
                                       );

  pPostionCharacteristic  = pService->createCharacteristic(
                      POSITIONCHARACTERISTIC_UUID,
                      BLECharacteristic::PROPERTY_READ   |
                      BLECharacteristic::PROPERTY_WRITE  |
                      BLECharacteristic::PROPERTY_NOTIFY |
                      BLECharacteristic::PROPERTY_INDICATE
                    );
                                       
  pPostionCharacteristic->addDescriptor(new BLE2902());

   
  pPauseCharacteristic->setCallbacks(new BlePauseCallback());
  pFilterCharacteristic->setCallbacks(new BleFilterCallback());  
  pService->start();

  BLEAdvertising *pAdvertising = BLEDevice::getAdvertising();
  pAdvertising->addServiceUUID(SERVICE_UUID);
  pAdvertising->setScanResponse(true);
  pAdvertising->setMinPreferred(0x06);  
  pAdvertising->setMinPreferred(0x12);
  BLEDevice::startAdvertising(); 
}

//start here
void setup(){
 
  Serial.begin(250000); 
  initConfigStorage();
  loadFilterAxis();
  setupBle();

  //setup estop/pause button 
  pinMode(ESTOPPIN, INPUT_PULLUP);
  debouncedEStop.attach(ESTOPPIN);
  debouncedEStop.interval(5); 

  //check if we already do have the estop depressed, so we do not take in data when we should not.
  //uncomment  debugnoestop during bench debugging 
  #ifdef DEBUG_NO_ESTOP 
    isPausedEStop = false;//!debouncedEStop.read();
  #endif
  Serial.print("init Estop check:");
  Serial.println(isPausedEStop);
         
  //if debugging make the pulse train very slow, so we can visually see the incrementing values in output
  #ifdef DEBUG_MOTORS
    microInterval = MICRO_INTERVAL_SLOW;
    Serial.println("Motor debug mode active!");
  #endif
  
  xMutex = xSemaphoreCreateMutex();
 
  xTaskCreatePinnedToCore(
                    InterfaceMonitorCode,   /* Task function. */
                    "InterfaceMonitor",     /* name of task. */
                    10000,       /* Stack size of task */
                    NULL,        /* parameter of the task */
                    1,           /* priority of the task */
                    &InterfaceMonitorTask,      /* Task handle to keep track of created task */
                    0);          /* pin task to core 0 */                  

  xTaskCreatePinnedToCore(
                    GPIOLoop,   /* Task function. */
                    "GPIOLoopTask",     /* name of task. */
                    10000,       /* Stack size of task */
                    NULL,        /* parameter of the task */
                    1,           /* priority of the task */
                    &GPIOLoopTask,      /* Task handle to keep track of created task */
                    1);          /* pin task to core 1 */
   
  outputBank.begin();

   //setup the outputs for the AC servo controllers
  setupPWMpins();

  //Timer for watchdog reset
  wtmr = xTimerCreate("wtmr", pdMS_TO_TICKS(1000), pdFALSE, (void*)0, reinterpret_cast<TimerCallbackFunction_t>(ping));
  xTimerStart(wtmr, 0);
}

void setupPWMpins() {
   
    //pins to use for pin state on reset
    for(int i=0;i<6;i++)
    {
        motors[i].stepPin = stepPins[i];
        motors[i].dirPin = dirPins[i];
        motors[i].pinState = false;
        motors[i].currentpos = 0;
        motors[i].targetpos = 0;

        outputBank.pinMode( motors[i].stepPin, OUTPUT );
        outputBank.pinMode( motors[i].dirPin, OUTPUT );
     }
}
  
//pulse train for step and direction, builds output to multiplexer
void handleStepDirection() {

  currentMicros = esp_timer_get_time();
  int dif = currentMicros - previousMicros;

  //creates the pulses in realtime, if enough time has passed.
  if (dif >= microInterval) {
        if (pinState) {
          
          //we need to bring the step pins down from what they where.
          //keep the direction the same, 
          pinState = false;

          //lock access to motor array
          xSemaphoreTake( xMutex, portMAX_DELAY );

          for(int i =0;i<6;i++)
          {
            motorStepDirValue = BIT_CLEAR(motorStepDirValue,stepPins[i]);
            motorStepDirValue2 = BIT_CLEAR(motorStepDirValue2,stepPins[i]);
          }
          
           //give access back up
          xSemaphoreGive( xMutex );

          outputBank.digitalWrite(motorStepDirValue);      
        
        } else { 
            pinState = true;

            //lock access to motor array
            xSemaphoreTake( xMutex, portMAX_DELAY );

            //set direction pins first
            for(int i =0;i<6;i++)
            {
              if(motors[i].currentpos > motors[i].targetpos)
              {
                 motorStepDirValue = BIT_CLEAR(motorStepDirValue,dirPins[i]);
                 motorStepDirValue2 = BIT_CLEAR(motorStepDirValue2,dirPins[i]);
              }
              else if(motors[i].currentpos < motors[i].targetpos)
              { 
                motorStepDirValue = BIT_SET(motorStepDirValue,dirPins[i]);
                motorStepDirValue2 = BIT_SET(motorStepDirValue2,dirPins[i]);
              }
            }
            
            //Next, set the step pins
            for(int i =0;i<6;i++)
            {
              if(motors[i].currentpos > motors[i].targetpos)
              {
                  motors[i].currentpos--;
                  motorStepDirValue2 = BIT_SET(motorStepDirValue2,stepPins[i]);
              }
              else if(motors[i].currentpos < motors[i].targetpos)
              { 
                  motors[i].currentpos++;
                  motorStepDirValue2 = BIT_SET(motorStepDirValue2,stepPins[i]);
              }
            }

            //print motor positions, and GPIO request bit array 
            #ifdef DEBUG_MOTORS
   
              for(int i=0;i<6;i++)   
              {
                Serial.print(motors[i].currentpos);
                Serial.print(",");
              }
                  
              Serial.println("");
         
            #endif
     
            //give access back up
            xSemaphoreGive( xMutex );

            //two outputs, one to set direction, one to then( reafirm direction + step)
            outputBank.digitalWrite(motorStepDirValue);     
            outputBank.digitalWrite(motorStepDirValue2);      
        }
        
        previousMicros = currentMicros;         
  }
}

void loop()
{      
}

//reads the serial line,  x,y,z,RX,RY,RZX, Where X is used to indicate end of line. 
//else data will buffer and parsed once a full line is available.
void processIncomingByte (const byte inByte)
{
    static char input_line [MAX_INPUT];
    static unsigned int input_pos = 0;
  
    switch (inByte)
    {
        case 'X':   // end of text
          input_line [input_pos] = 0;  // terminating null byte
          process_data (input_line);          
          input_pos = 0;  
          break;
        case '\r':   // discard carriage return
          break;
        
        default:
          //buffer data
          if (input_pos < (MAX_INPUT - 1))
            input_line [input_pos++] = inByte;
          break;
    } 
} 

//check estop button often, will flip estop variable when button changes
void checkEStop(){

  //Update button status through debounce filter
  debouncedEStop.update();

  // Get the updated value :
  int value = debouncedEStop.read();

  if ( debouncedEStop.fell() ) {  // Call code if button transitions from HIGH to LOW
     pauseEStop();
  }

   if ( debouncedEStop.rose() ) {  // Call code if button transitions from HIGH to LOW
      resumeEStop();
   } 
}

void resumeEStop(){
    isPausedEStop = false;
    isRateLimiting = true;
    
    Serial.print("Estop:");
    Serial.println(isPausedEStop);
}

void pauseEStop(){ 
     isPausedEStop = true;
     isRateLimiting = false;
    
     Serial.print("Estop:");
     Serial.println(isPausedEStop);

}

//notify method for Ble service, if a device is connected will send periodic motor position data,
void checkBleNotify(){

  currentMicrosBle  = esp_timer_get_time();
  int dif = currentMicrosBle  - previousMicrosBle ;

  //creates the pulses in realtime, if enough time has passed.
  if (dif >= MICRO_INTERVAL_BLE_SEND ) {
    
    if (deviceConnected) {
        
        //lock access to motor array
        xSemaphoreTake( xMutex, portMAX_DELAY );
            
        String output;
        for(int i=0;i<6;i++)   
        {
          output +=  String(motors[i].currentpos);
        
          if(i<5)
            output +=",";
        }
               
        //give access back up
        xSemaphoreGive( xMutex );
            
        pPostionCharacteristic->setValue(output.c_str());
        pPostionCharacteristic->notify();
    }

    previousMicrosBle  = currentMicrosBle;         
  }
}

//Thread that handles reading from PC uart
void InterfaceMonitorCode( void * pvParameters ){
  for(;;){
    
    while (Serial.available () > 0)
      processIncomingByte (Serial.read ());
   
    checkEStop();
    checkBleNotify();
  } 
}

//Thread/loop that handles generating pulses for swing arm movement.
void GPIOLoop( void * pvParameters ){
  for(;;){
      handleStepDirection();   
  }
}

bool initConfigStorage() {
  return preferences.begin(NAMESPACE, false);
}

int getAxis1Filter() {
  return preferences.getInt(AXIS1_KEY, 100);
}

void setAxis1(int value) {
  preferences.putInt(AXIS1_KEY, value);
}

int getAxis2Filter() {
  return preferences.getInt(AXIS2_KEY, 100);
}

void setAxis2(int value) {
  preferences.putInt(AXIS2_KEY, value);
}

int getAxis3Filter() {
  return preferences.getInt(AXIS3_KEY, 100);
}

void setAxis3(int value) {
  preferences.putInt(AXIS3_KEY, value);
}

int getAxis4Filter() {
  return preferences.getInt(AXIS4_KEY, 100);
}

void setAxis4(int value) {
  preferences.putInt(AXIS4_KEY, value);
}

int getAxis5Filter() {
  return preferences.getInt(AXIS5_KEY, 100);
}

void setAxis5(int value) {
  preferences.putInt(AXIS5_KEY, value);
}

int getAxis6Filter() {
  return preferences.getInt(AXIS6_KEY, 100);
}

void setAxis6(int value) {
  preferences.putInt(AXIS6_KEY, value);
}

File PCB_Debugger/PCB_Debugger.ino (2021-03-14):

#include <SPI.h>
#include "MCP23S17.h"


SPIClass hspi( HSPI );
MCP23S17 outputBank( &hspi, 15, 0 );


#define BIT_SET(a,b) ((a) |= (1ULL<<(b)))
#define BIT_CLEAR(a,b) ((a) &= ~(1ULL<<(b)))


//mcp1
const int stepPins[] = {8,9,10,11,12,13};   
const int dirPins[] = {14,15,0,1,2,3};


void setup() {  
  Serial.begin(115200);
   outputBank.begin();

    for (int8_t i = 0; i <= 15; i++) {
     outputBank.pinMode( i, OUTPUT );
   }
}

int64_t currentMicros = esp_timer_get_time();
int64_t previousMicros = 0;
int microInterval = 1000000;//2 sec?

int state = 0;
void loop() {

  uint16_t motorStepDirValue = 0;   
  currentMicros = esp_timer_get_time();
  int elapsedTime = currentMicros - previousMicros;

  // check to see if we need to increment our PWM counters yet
  if (elapsedTime >= microInterval) {
    
      if(state == 0)
      {
          for(int i =0;i<6;i++){         
            motorStepDirValue = BIT_SET(motorStepDirValue,stepPins[i]);
            motorStepDirValue = BIT_SET(motorStepDirValue,dirPins[i]);
          }
        
        state = 1;
      }
      else
      {
        state = 0;
      }

        Serial.println("Outputs");
        for (byte i=0; i<16; i++) {
          byte state = bitRead(motorStepDirValue, i);
          Serial.print(state);
        }
        
        Serial.println("");

      outputBank.digitalWrite(motorStepDirValue);

      previousMicros = currentMicros;
  }
}

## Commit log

2020-11-08 Added Kompas 3D drawings
    [StewartPlatformSimulator.xlsm]
2020-11-29 I've added new schematic
    [111.kicad_pcb, 111.sch, BOM_Controller.csv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]
2020-11-30 PCB updated
    [111-B_Cu.gbr, 111-B_Mask.gbr, 111-B_Paste.gbr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]
2020-12-03 PCB was changed
    [111-B_Cu.gbr, 111-B_Mask.gbr, 111-B_SilkS.gbr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]
2020-12-03 I've renamed folders
    [111-B_Paste.gbr, 111-NPTH.drl, 111-PTH.drl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]
2020-12-03 project updated
    [6dof_controller-B_Cu.gbr, 6dof_controller-B_Mask.gbr, 6dof_controller-B_Paste.gbr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]
2020-12-04 I've added illustation for technical
    [6dof_controller.sch]
2020-12-05 The circuit and board were redesigned after prototyping. Removed all unnecessary. Reduced the PCB.
    [6dof_controller-B_Cu.gbr, 6dof_controller-B_Mask.gbr, 6dof_controller-B_Paste.gbr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]
2020-12-05 Added PCB image
    [6dof_controller.kicad_pcb, 6dof_controller.sch]
2020-12-10 I've added dwg files for laser cut
    [base_part1.dwg, base_part1_support.dwg, base_part2.dwg]
2020-12-15 Add schematic for wheel
    [wheel.kicad_pcb, wheel.sch]
2021-01-06 I've added schematic for MMOS FFB
    [Wheel.kicad_pcb, Wheel.sch]
2021-01-06 I've modified wheel's schematic and pcb
    [Wheel.kicad_pcb, Wheel.sch]
2021-01-06 I've modified wheel's PCB
    [Wheel.kicad_pcb, Wheel.sch]
2021-01-07 TDD Wheel's was changed
    [Wheel.kicad_pcb, Wheel.sch]
2021-01-08 Wheel's PCB changed
    [Wheel.kicad_pcb, Wheel.sch, wheel.sch]
2021-01-08 I've modify TDD's PCB.
    [Wheel.kicad_pcb]
2021-01-08 TDD's PCB was changed
    [Wheel.kicad_pcb]
2021-01-09 I've added pedals board
    [Pedals.kicad_pcb, Pedals.sch]
2021-01-10 I've modified Pedal's PCB. I've added gerber files
    [Pedals.kicad_pcb, Pedals.sch]
2021-01-10 I've added drawing for arm tube
2021-01-16 I've modified schematic and PCB for 6DOF controller
    [6dof_controller-B_Cu.gbr, 6dof_controller-B_Mask.gbr, 6dof_controller-B_Paste.gbr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]
2021-01-18 I've added a connector for connect STM32F407G-DISK1 to the Wheel board
    [Wheel.kicad_pcb, Wheel.sch]
2021-01-18 Wheel's scheme updated
    [Wheel.kicad_pcb, Wheel.sch]
2021-01-18 I've added rear button for logitech h shifter
    [Wheel.kicad_pcb, Wheel.sch]
2021-01-18 I've modified Wheel's scheme and PCB
    [Wheel.kicad_pcb, Wheel.sch]
2021-01-26 I've added supressors for all buttons in the Wheel board
    [Wheel.kicad_pcb, Wheel.sch]
2021-01-26 I've chenged sil layer in the Wheel board
    [Wheel.kicad_pcb]
2021-01-28 I've changed wheel's PCB, I've added GERBER files
    [Wheel.kicad_pcb, Wheel.sch]
2021-03-14 I've changed the drawings
    [base_part1.dxf, base_part1_support.dxf, base_part2.dxf]

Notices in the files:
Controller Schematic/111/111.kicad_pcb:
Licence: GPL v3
